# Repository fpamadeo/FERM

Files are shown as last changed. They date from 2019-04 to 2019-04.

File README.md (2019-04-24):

# F.E.R.M.

## UIC ECE Senior Design 2018-2019

_______________________________________________________________________________________________________________________________
## Table of Contents:
**FERMix** | **Fryer**
:---: | :---
**1** | [Members](README.md#1-Members)
**2** | [About the Project](README.md#2-About-the-Project)
2.1 | [Abstract](README.md#21-Abstract)
2.2 | [Project Overview](README.md#22-Project-Overview)
2.3 | [Design Alternatives](README.md#23-Design-Alternatives)
2.4 | ["Final Design"](README.md#24-Final-design)
2.5 | [Conclusion](README.md#25-Conclusion)
**3** | [Construction Guide](README.md##3-Construction-Guide)
3.1 | [LCD Screen](README.md#31-LCD-Screen)
3.2 | [Ultrasonic Sensor](README.md#32-Ultrasonic-Sensor)
3.3 | [Motor Driver](README.md#33-Motor-Driver)
3.4 | [Keypad](README.md#34-keypad)
**4** | [Acknowledgements](README.md##4-Acknowledgements)
 
____________________________________________________________________
## 1. Members:
* Francis Paul Amadeo
* Erick Estrada
* Meshal Alsaeed
* Rami Muhammad
______________________________________________________
## 2. About the Project:
### 2.1 Abstract:
>The project aims to create an affordable system for all commercial-grade fryers. In regards to cook-time management, we wish to ease the cooks’ workload by automating the deep frying process. However, we do not want our project to interfere with their normal operation while frying. Our project would just be a failsafe so that the food does not get overcooked. To solve these objectives, we opted to go for a modular design, which will include the main system and extensions. The main system will be chain-driven. The extensions can be customized depending on the user’s needs and space. Also, this design will feature pre-set and configurable user settings. Thus, giving the cooks a less stressful environment, making them free to do more things in the kitchen. The system is designed primarily as a way to simplify and reduce the complexity of frying food for restaurants by taking into account the FDA’s regulations.

### 2.2 Project Overview:
>The goal is to build an add-on for restaurant deep fryers. This add-on would automate the lowering and raising of the frying basket, with the user inputting how long the deep frying will last. Due to the stressful environment of restaurant kitchens, there are lots of food that get  burned from being left alone for too long. With our add-on, food waste would be reduced in addition to simplifying the frying process for workers.

### 2.3 Design Alternatives:
**Mechanisms:**
>The Actuator would help decrease the bulkiness of our system. However, this would also limit the modularity of the system, compared to the chain driven design we opted for.
> 
>The Lead Screw would give us a high positioning accuracy, but would in turn, be inefficient. Furthermore, lead screws are significantly more expensive compare to the other designs we had in mind

**Sensors:**
>A magnetic switch would be a great sensor to detect when the fryer basket is on our hanger, since most likely the basket is made of metal. However, since the hanger is made of metal itself, we opted to not use a magnetic switch.
>
>Similar to a magnetic switch, an inductive sensor will detect when metal object is near it. But rather than having a 0 or 1 input, it can sense how far the nearest metal is. Unfortunately, we opted to use the sensor we already have on-hand so we could use the resources for elsewhere. Going forward, we would have went with this sensor.

### 2.4 "Final Design":
>For the final design, we are going  to use a chain-driven mechanism, with one of the links of the chains attached to a steel pipe with threaded ends. This end could then be attached to a various choice of connectors which in turn, be connected to other pipes and finally to the fryer basket hanger. This gives the user the ability to customize the connections in accordance with their need. Furthermore, other than the basic timer option, the system gives the user the options to save up to three preset times and to calibrate the depth of the fryer vat.

### 2.5 Conclusion:
>In hindsight, with the large mechanical aspect of our system, we would have benefited with consulting with more mechanical engineers with our design. We would have also hoped to be able to test our other design alternatives, and be able to pick which one is the best.
> 
>Going forward, we have some design changes in order to improve the overall functionality and appearance of the system. These changes would include: a mechanism to prevent the chain from slacking as weight is added to the system; inductive sensing instead of ultrasonic; metal housing; a more permanent wiring and circuit layout and; other relatively minor issues we have yet to tackle due to time and financial constraints. 

______________________________________________________
## 3. Construction Guide:
* We are using an Arduino Mega (Elegoo MEGA2560 R3)
* We are using the MD10C R3 Motor Driver
### 3.1 LCD Screen:
Arduino | 2x16 LCD 
--- | ---
GND | VSS
5V | VDD
GND -> 1kOhm Resistor | VO
D12 | RS
GND | RW
D11 | E 
D23 | DB0
D27 | DB1
D31 | DB2
D35 | DB3
D34 | DB4
D30 | DB5
D26 | DB6
D22 | DB7
5V -> 224Ohm | A
GND | K

### 3.2 Ultrasonic Sensor:
Arduino | HC-SR04 
--- | ---
GND | GND
D48 | ECHO
D49 | TRIGGER
5V | VCC

### 3.3 Motor Driver:
Arduino | MD10C R3
--- | ---
GND | GND
D13 | PWM
D53 | DIR

### 3.4 Keypad:
Arduino | Keypad
--- | ---
D2 | 1
D3 | 2
D4 | 3
D5 | 4
D6 | 5
D7 | 6
D8 | 7
D9 | 8

***\*Keypad pins are numbered left to right, from the POV of looking at the back upright\****

______________________________________________________
## 4. Acknowledgements:
>Team F.E.R.M. would like to thank: the staff of UIC’s Makerspace; the members of Chicago Engineering Design Team; Mona Hurt and; our advisor, Dr. Wenjing Rao.

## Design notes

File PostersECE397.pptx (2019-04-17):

## FERMix Francis Amadeo, Erick Estrada, Rami Muhammed, Meshal Alsaeed, Advisor: Dr. Wejing Rao

Abstract

The project aims to create an affordable system for all commercial-grade fryers. In regards to cook-time management, we wish to ease the cooks’ workload by automating the deep frying process. However, we do not want our project to interfere with their normal operation while frying. Our project would just be a failsafe so that the food does not get overcooked. To solve these objectives, we opted to go for a modular design, which will include the main system and extensions. The main system will be chain-driven. The extensions can be customized depending on the user’s needs and space. Also, this design will feature pre-set and configurable user settings. Thus, giving the cooks a less stressful environment, making them free to do more things in the kitchen. The system is designed primarily as a way to simplify and reduce the complexity of frying food for restaurants by taking into account the FDA’s regulations.

Project Overview

Engineering Requirements

- The device should be able to operate from a 12V source
- The system should move the frying basket up and down in a range of 1.5 ft
- No part of the system should ever be dipped in the oil
- System should be easily disassembled with the use of handheld tools.
- The system will have a 4x4 keypad user-interface

Final Design

Design Alternatives

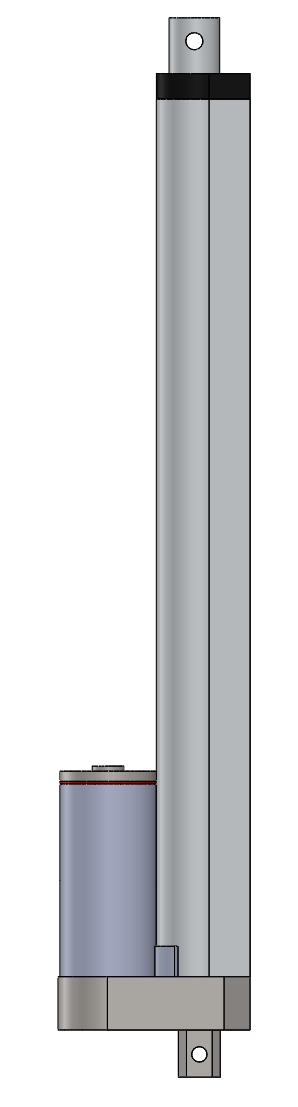
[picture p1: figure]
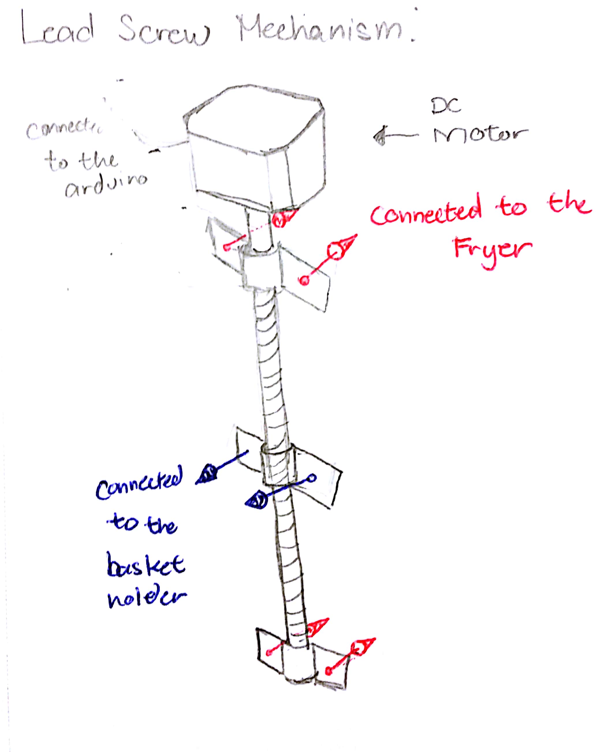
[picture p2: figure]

Testing & Results

Mechanisms:

Sensors:

Actuator

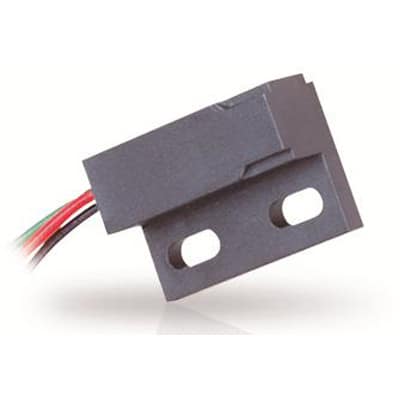
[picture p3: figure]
ZF Electronics MP102103

Magnetic switch

Lead Screw

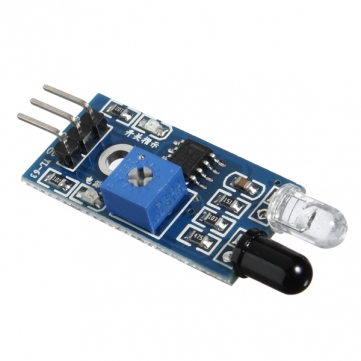
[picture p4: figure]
Image result for infrared proximity sensor arduino

Infrared
Proximity

Conclusion

Acknowledgements

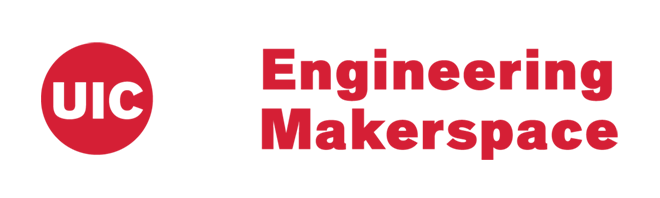
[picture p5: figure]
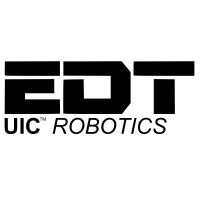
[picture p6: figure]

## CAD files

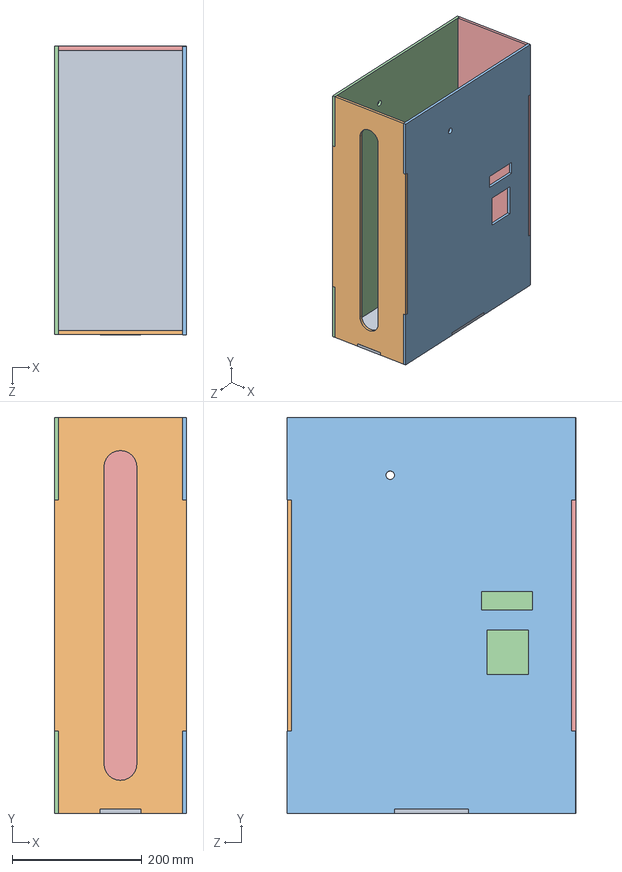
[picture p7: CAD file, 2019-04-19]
CAD/allpartstogether.SLDASM
203.4 x 609.9 x 444.7 mm
bottompanel
frontpanel
rightpanel
leftpanel
backpanel

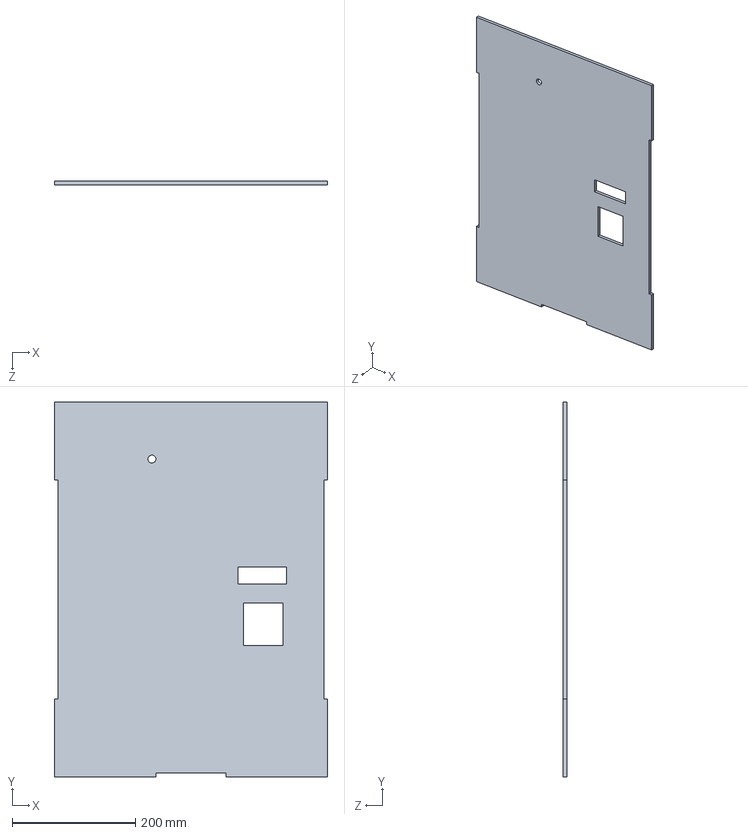
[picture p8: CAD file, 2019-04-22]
CAD/rightpanel.SLDPRT
444.5 x 609.6 x 6.35 mm

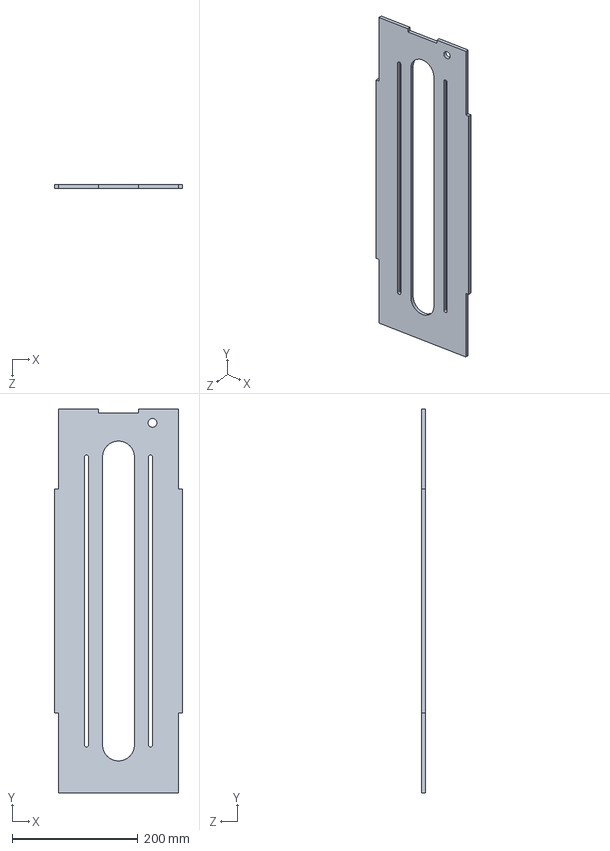
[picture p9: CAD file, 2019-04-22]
CAD/frontpanel.SLDPRT
203.2 x 609.6 x 6.35 mm

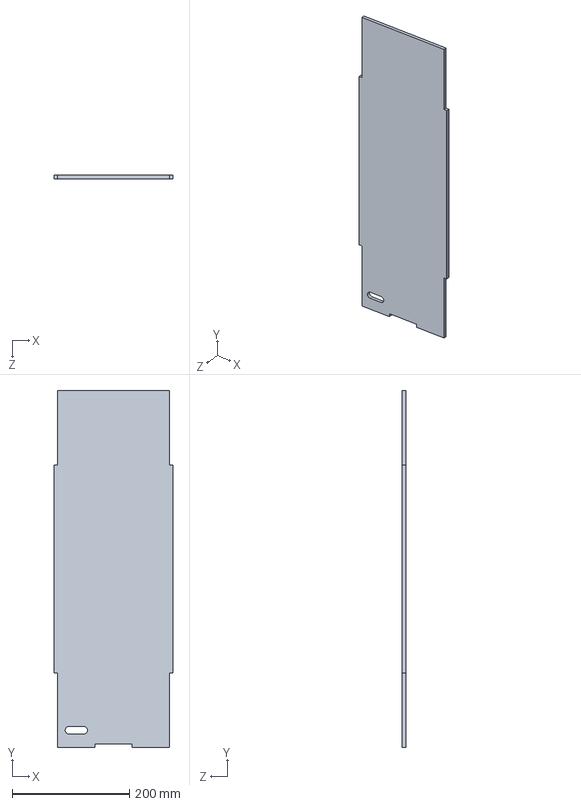
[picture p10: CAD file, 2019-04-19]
CAD/backpanel.SLDPRT
203.2 x 609.6 x 6.35 mm

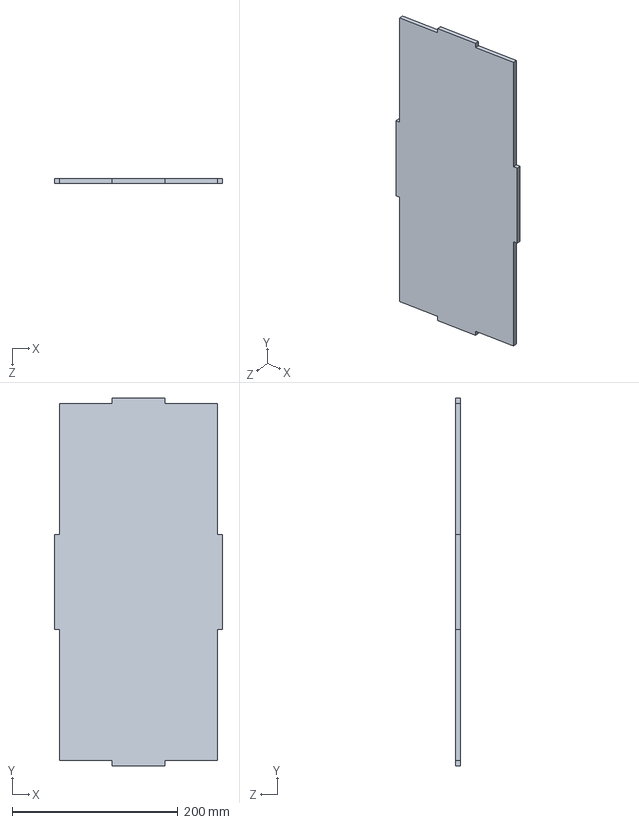
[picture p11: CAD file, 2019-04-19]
CAD/bottompanel.SLDPRT
203.2 x 444.5 x 6.35 mm

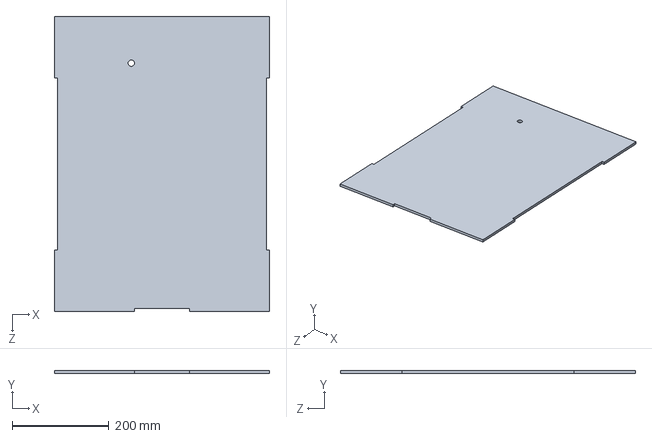
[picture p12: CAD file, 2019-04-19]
CAD/leftpanel.SLDPRT
444.5 x 6.35 x 609.6 mm

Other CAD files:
CAD/backpanel.DXF
CAD/bottompanel.DXF
CAD/frontpanel.DXF
CAD/leftpanel.DXF
CAD/rightpanel.DXF

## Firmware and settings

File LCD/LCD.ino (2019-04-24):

#include <LiquidCrystal.h>
#include <Wire.h>
#include <Keypad.h>
//**********************************************************************************************************//
//Preset:
String preset[3] = {"0015","0030","0100"}; //"MMSS" //Preset times

//LCD pins:
const int rs = 12, en = 11, d0 = 23, d1 = 27, d2 = 31, d3 = 35, d4 = 34, d5 = 30, d6 = 26, d7 = 22;
LiquidCrystal lcd(rs, en, d0, d1, d2, d3, d4, d5, d6, d7);

//MOTOR:
#define pwmPin 13 //Pin to send how fast it is
#define dirPin 53 //Pin to send if going clockwise or counter-clockwise
#define UP true //boolean value to send to move up
#define DOWN false //boolean value to send to move down
#define MOTOR_DELAY 200 //how long is each "step"; in microseconds
#define MOTOR_SPEED 255 //PWM value to send to motor driver; Range: 0-255
#define DEFAULT_STEPS 10//From lowest point to highest point in steps

//ULTRASONIC(US)  SENSOR:
#define echoPin 48 //ECHO
#define trigPin 49 //TRIGGER
#define sensorDelay 50 //centiseconds 
#define sensorThres 10 //threshold 

//Keypad:
const byte ROWS = 4; //How many rows are there in the keypad
const byte COLS = 4; //How many columns are there in the keypad

char keys[ROWS][COLS] =  //Mapping out the corresponding characters for each key
{
  {'1','2','3','A'},
  {'4','5','6','B'},
  {'7','8','9','C'},
  {'*','0','#','D'}
};

byte rowPins[ROWS] = {9, 8, 7, 6}; 
byte colPins[COLS] = {5, 4, 3, 2};

Keypad userKeypad = Keypad(makeKeymap(keys), rowPins, colPins, ROWS, COLS);

//GLOBAL Variables:

//Strings:
String timeIN = "0000"; //Time input in by the user for "normal" executions
String tempTime = "0000"; //Time input in by the user for "shift" executions; ##TODO: Might be redundant##

//Ints
int timeLeft = 0; //The actual time the user enters; should always be in seconds
int selected = 0; //The preset the user selected to be changed
int blinkDelay = 0; //Used to make the timer blink every 1 second
long duration;     //How long til the signal comes back
int distance;      //How far til the signal bounces off of something
int stepsToDo = DEFAULT_STEPS; //Steps needed for now #TODO#
int tempSteps = 0; //Steps the user is doing before everything is saved or cancelled 

//Bool:
bool error = false; //USED TO CHECK FOR ERRORS, should never be true
bool cancel = false; //TRUE when user cancels current action/s
bool shift = false; //TRUE when user uses the shift key 
bool calibrate = false; //TRUE when the user is calibrating
bool changePreset = false; //TRUE when the user is changing a preset
bool blinkTime = false; //USED FOR MAKING THE TIME BLINK every 1 second 

//**********************************************************************************************************//
//SETUP
void setup() 
{
  //US SENSOR:
  pinMode(trigPin, OUTPUT); // Sets the trigPin as an Output
  pinMode(echoPin, INPUT); // Sets the echoPin as an Input

  //MOTOR:
  pinMode(dirPin, OUTPUT);
  digitalWrite(dirPin, HIGH);//initialization
  analogWrite(pwmPin, 0); //initialization
  stepsToDo = DEFAULT_STEPS;
   
  //TESTING:
  Serial.begin(9600);

  //LCD:
  // set up the LCD's number of columns and rows:
  lcd.begin(16, 2);
  // Print a message to the LCD.
  lcd.print("Standby");
  lcd.setCursor(11,0);    
  lcd.print("TIME:");
  lcd.setCursor(11,1);    
  lcd.print(timeIN[0]);
  lcd.print(timeIN[1]);
  lcd.print(":");
  lcd.print(timeIN[2]);
  lcd.print(timeIN[3]);
}

//**********************************************************************************************************//
//Previous Code:
/*
//MOTOR GO UP
void moveUp(){
  digitalWrite(dirPin, HIGH);
  analogWrite(pwmPin, 255);
  delay(100);
}

//MOTOR GO DOWN
void moveDown(){
  digitalWrite(dirPin, LOW);
  analogWrite(pwmPin, 255);
  delay(100);
}
*/

//MOVE MOTOR:
void moveMotor(bool dir, int steps){
  int eachDelay;
  if (steps < 1){
    error = true;
    updateScreen(); //Show on screen, there's error
    delay(3000);
    updateScreen(); //Return to standby, after three second
    return;
  }
  if (dir == UP){
    digitalWrite(dirPin, LOW);
    eachDelay = MOTOR_DELAY;
  }
  else{
    digitalWrite(dirPin, HIGH);
    eachDelay = MOTOR_DELAY * 80 / 100;
  }
  analogWrite(pwmPin, MOTOR_SPEED);
  delay(eachDelay * (steps));
  //analogWrite(pwmPin, MOTOR_SPEED / 2);
  //delay(MOTOR_DELAY);
  analogWrite(pwmPin, 0);
  return;
}

//**********************************************************************************************************//
//UPDATES JUST TIME
void updateTime(){
  //lcd.setCursor(0,1);
  //lcd.print(timeLeft);
  int minutes, seconds;
  if(cancel){
    return;
  }
  minutes = timeLeft / 60;
  seconds = timeLeft % 60;
  if(minutes > 99){
    minutes = 99;
  }
  lcd.setCursor(11,1);    
  lcd.print(minutes/10);
  lcd.print(minutes%10);
  lcd.print(":");
  lcd.print(seconds/10);
  lcd.print(seconds%10);
  delay(1000);
}

//UPDATES DISPLAY
void updateScreen(){
  if (error){
    error = false;
    lcd.setCursor(11,1);
    lcd.print("ERROR");
    delay(1000);
  }
  if (cancel){
    cancel = false;
    lcd.setCursor(11,1);
    lcd.print("CNCEL");
    lcd.setCursor(0,0);
    lcd.print("Standby    ");
    lcd.setCursor(0,1);
    lcd.print("           ");
    delay(500);
  }
  lcd.setCursor(0,1);
  if (changePreset){
    lcd.print("Preset");
    lcd.print(" ");
  }
  if (selected != 0){
    lcd.print(selected);
    lcd.print(" ");
  }
  if (shift){
    lcd.print("S");
  }
  if (timeLeft <= 0 or cancel){
    lcd.setCursor(11,1);    
    lcd.print(timeIN[0]);
    lcd.print(timeIN[1]);
    lcd.print(":");
    lcd.print(timeIN[2]);
    lcd.print(timeIN[3]);
  }
  else{
    lcd.setCursor(0,0);
    lcd.print("ON         ");
  }
}

//**********************************************************************************************************//
//GIVES PROPER INT FOR CASES:
String getInt(char input){
  if (input == '*'){
    return "10";
  }
  if (input == '#'){
    return "11";
    }
  if (input == 'A'){
    return "12";
  }
  if (input == 'B'){
    return "13";
    }
  if (input == 'C'){
    return "14";
  }
  if (input == 'D'){
    return "15";
  }
  String returnThis = "";
  returnThis += input;
  return returnThis;
}

//**********************************************************************************************************//

//CHECKS SENSOR IF THERE IS SOMETHING THERE //#TODO: FIND DECENT NUMBER FOR THE BASKET#//
bool checkSensor(bool motorPosition){

  for(int i = 0; i < sensorDelay; i++){
       // Clears the trigPin
      digitalWrite(trigPin, LOW);
      delayMicroseconds(2);
      // Sets the trigPin on HIGH state for 10 micro seconds
      digitalWrite(trigPin, HIGH);
      delayMicroseconds(10);
      digitalWrite(trigPin, LOW);
      // Reads the echoPin, returns the sound wave travel time in microseconds
      duration = pulseIn(echoPin, HIGH);
      // Calculating the distance
      distance= duration*0.034/2;
      // Prints the distance on the Serial Monitor
      Serial.print("Duration: ");
      Serial.println(duration);
      Serial.print("Distance: ");
      Serial.println(distance);
      if (motorPosition == UP){
        if (distance < sensorThres){
          return false;
        }
      }
      else{
        if (distance < sensorThres){
          return true;
        }
      }
      
  }
  if (motorPosition == UP){
        return true;
   }
  else{
        return false;
    }
}

//**********************************************************************************************************//
//CHECKS KEY AND CORRESPONDS THE RIGHT ACTION
void checkKey(int input){
  switch(input){
   case 11: //Cancel?
      //Use Function to cancel timer here
      cancel = true;
      timeIN = "0000";
      timeLeft = 0;
      
      updateScreen();
      break;
   case 12: //Shift fn?
      shift = true;
      updateScreen();
      //lcd.setCursor(0,0);
      //lcd.print("SHIFT");
      break;case 13: //Preset 1?
      lcd.setCursor(0,0);
      timeIN = preset[0];
      updateScreen();
      break;
   case 14: //Preset 2?
      lcd.setCursor(0,0);
      timeIN = preset[1];
      updateScreen();
      break;
   case 15: //Preset 3?
      lcd.setCursor(0,0);
      timeIN = preset[2];
      updateScreen();
      break;
    case 1:
    case 2:
    case 3:
    case 4:
    case 5:
    case 6:
    case 7:
    case 8:
    case 9:
    case 0:
      //Remove the first char of the string and add the input at the end:
      timeIN.remove(0,1);
      timeIN += input;
  
      updateScreen();
      break;
   case 10: //Enter?
      //use function to start timer here
      String toNum = "";
      toNum += timeIN[0];
      toNum += timeIN[1];
      timeLeft =  toNum.toInt() * 60;
      toNum = "";
      toNum += timeIN[2];
      toNum += timeIN[3];
      timeLeft = timeLeft + toNum.toInt();
      timeIN = "0000";
      updateScreen();
      break;
   default: 
      error = true;
      break;
  }
}

//CHECKS KEY AND CORRESPONDS THE RIGHT SHIFT ACTION
void checkShift(int input){
  //lcd.print(input);
  switch(input){
    case 1://Calibration
      if(not changePreset){
        calibrate = true;
        lcd.setCursor(0,0);
        lcd.print("Calibrate  ");
        updateScreen();
      }
      break;
    case 2:
      if (calibrate){
        moveMotor(UP, 1);
        tempSteps--;
      }
      break;
    case 5:
      if (calibrate){
        moveMotor(DOWN,1);
        tempSteps++;
      }
      break;
    case 4://Change Preset
      if(not calibrate){
        changePreset = true;
        lcd.setCursor(0,0);
        lcd.print("Changing ");
        updateScreen();
      }
      break;
    case 10: //Enter?
      calibrate = false;
      changePreset = false;
      shift = false;
      if (tempSteps < 0){
        tempSteps--;
      }
      else if (tempSteps > 0){
        tempSteps++;
      }
      stepsToDo += tempSteps;
      tempSteps = 0;
      lcd.setCursor(0,0);
      lcd.print("Saved      ");
      delay(500);
      lcd.setCursor(0,0);
      lcd.print("Standby    ");
      lcd.setCursor(0,1);
      lcd.print("           ");
      break;
   case 11: //Cancel?
      if(tempSteps > 0){
        for(int i = 1; i <= tempSteps; i++){
          moveMotor(UP, 1);
          delay(100);
        }
      }
      else if(tempSteps == 0){
        
      }
      else{
        for(int i = 1; i <= (tempSteps*-1) ; i++){
          moveMotor(DOWN, 1);
          delay(100);
        }
      }
      tempSteps = 0;
      calibrate = false;
      changePreset = false;
      shift = false;
      lcd.setCursor(0,0);
      lcd.print("Cancelled  ");
      delay(500);
      lcd.setCursor(0,0);
      lcd.print("Standby    ");
      lcd.setCursor(0,1);
      lcd.print("           ");
      
      break;
   case 13: //Preset 1?
      if(changePreset){
        selected = 1;
        tempTime = "0000";
      }
      updateScreen();
      break;
   case 14: //Preset 2?
      if(changePreset){
        selected = 2;
        tempTime = "0000";
      }
      updateScreen();
      break;
   case 15: //Preset 3?
      if(changePreset){
        selected = 3;
        tempTime = "0000";
      }
      updateScreen();
      break;
   default:
      break;
  }
}

//Uses the whole keypad again, for changing presets
void changeSelected(int input){
  if (changePreset){
      switch(input){
       case 13: //Preset 1?
          if(changePreset){
            selected = 1;
            tempTime = "0000";
          }
          updateScreen();
          break;
       case 14: //Preset 2?
          if(changePreset){
            selected = 2;
            tempTime = "0000";
          }
          updateScreen();
          break;
       case 15: //Preset 3?
          if(changePreset){
            selected = 3;
            tempTime = "0000";
          }
          updateScreen();
          break;
        case 11: //Cancel?
          //Use Function to cancel timer here
          selected = 0;
          shift = false;
          lcd.setCursor(0,0);
          lcd.print("Cancellled  ");
          lcd.setCursor(0,1);
          lcd.print("           ");
          tempTime = "0000";
          updateScreen();
          break;
        case 1:
        case 2:
        case 3:
        case 4:
        case 5:
        case 6:
        case 7:
        case 8:
        case 9:
        case 0:
          //Remove the first char of the string and add the input at the end:
          //if(tempTime[selected-1] == "0"){
            tempTime.remove(0,1);
            tempTime += input;
          //}
          //else{
          //  error = true;
          //}
          updateScreen();
          break;
       case 10: //Enter?
          //use function to start timer here
          preset[selected-1] = tempTime;
          lcd.setCursor(0,0);
          lcd.print("DONE       ");
          lcd.setCursor(0,1);
          lcd.print("           ");
          shift = true;
          selected = 0;
          tempTime = "0000";
          break;

       default:
          error = true;
          break;
    }
  }
}

//**********************************************************************************************************//
//MAIN:
void loop() 
{
  //Getting input; customKey == NULL if there is none
  char customKey = userKeypad.getKey();
  //Check if there's an interrupt or there is time left:
  if (customKey){
    String caseKey = "";
    caseKey += getInt(customKey);
    int caseKeyInt = caseKey.toInt();
    Serial.println(customKey);
    
    //lcd.setCursor(0,0);
    //lcd.print(customKey);
    //lcd.print(":");
    //lcd.print(caseKeyInt);
    
    if (not shift){
       checkKey(caseKeyInt);
    }
    else{
      if(selected == 0){
        checkShift(caseKeyInt);
      }
      else{
        changeSelected(caseKeyInt);
      }
    }
  }

 if (timeLeft > 0){
    updateTime();
    timeLeft--;
    if (timeLeft == 0){
      lcd.setCursor(15,1);
      lcd.print("0");
      if(checkSensor(DOWN)){
        for(int i = 0; i < stepsToDo; i++){
          moveMotor(UP, 1);
          delay(10);
        }
        Serial.print("FRYER'S THERE");
        delay(500);
        lcd.setCursor(0,0);
        lcd.print("Hanger Up  ");
        lcd.setCursor(0,1);
        lcd.print("           ");
        while(not checkSensor(UP)){
        //  delay(200); //loop while basket is there
        }
        for(int i = 0; i < stepsToDo; i++){
          moveMotor(DOWN, 1);
          delay(10);
        }
      }
      else{
        lcd.setCursor(0,0);
        lcd.print("NO BASKET");
        delay(500);
      }
      lcd.setCursor(0,0);
      lcd.print("Standby  ");
      lcd.setCursor(0,1);
      lcd.print("           ");      
    }
 }
 if (changePreset){
    if (blinkTime){    
      lcd.setCursor(11,1);    
      lcd.print(tempTime[0]);
      lcd.print(tempTime[1]);
      lcd.print(":");
      lcd.print(tempTime[2]);
      lcd.print(tempTime[3]);
      if(blinkDelay >= 500){
        blinkTime = false;
        blinkDelay = 0;
      }
      else{
        blinkDelay++;
      }
    }
    else{
      lcd.setCursor(11,1);    
      lcd.print("     ");
      if(blinkDelay >= 500){
        blinkTime = true;
        blinkDelay = 0;
      }
      else{
        blinkDelay++;
      }
    }
 }

}

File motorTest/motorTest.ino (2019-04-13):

void setup() 
{
  pinMode(2, OUTPUT);
  // put your setup code here, to run once:

}

void loop() 
{
analogWrite(13, 255);






/*for (int i=0; i <= 255; i++)
{
      analogWrite(13, i);
      //delay(5000);
 }
delay(5000);


for (int i=255; i >= 255; i--)
{
      analogWrite(13, i);
      //delay(5000);
 }
delay(5000);
*/
/*
delay(500);
digitalWrite(1, HIGH);
analogWrite(13, 255);
delay(500);
analogWrite(13, 200);
delay(500);
analogWrite(13, 150);
delay(500);
analogWrite(13, 100);
delay(500);
analogWrite(13, 50);
delay(500);
analogWrite(13, 0);
delay(500);
*/

 /*
delay(1000);

digitalWrite(1, LOW);
for(int i=0; i<=255; i++)
{
  analogWrite(13, i);
  delay(10);
}
/////////
*/



/*
digitalWrite(1, HIGH);
for(int i=255; i>=0; --i)
{
  analogWrite(13, i);
  delay(10);
}

delay(2000);


digitalWrite(1, LOW);
for(int i=0; i<=0; i++)
{
  analogWrite(13, i);
  delay(10);
}

delay(3000);

/*
digitalWrite(1, LOW);
analogWrite(13, 0);
delay(500);
analogWrite(13, 50);
delay(500);
analogWrite(13, 100);
delay(500);
analogWrite(13, 150);
delay(500);
analogWrite(13, 200);
delay(500);
analogWrite(13,255);
delay(3000);
*/

/*
digitalWrite(1, HIGH);
for (int i = 255; i >= 0; --i) 
{
  analogWrite(13, i);
  delay(500);
}
 delay(2500);
 digitalWrite(1, LOW);

 for (int i= 0; i <=0; i++) 
{
  analogWrite(13, i);
  delay(500);
}
 delay(2500);
*/

/*
//delay(1000);
digitalWrite(1, LOW);

for (int i=0; i <= 255; i++)
{
  
      analogWrite(13, i);
      i=i+50;
    
 }
delay(2500);

*/


/*digitalWrite(1, LOW);
analogWrite(13, 50);
delay(500);
analogWrite(13, 100);
delay(500);
analogWrite(13, 150);
delay(500);
analogWrite(13, 200);
delay(500);
analogWrite(13, 255);
delay(10000);
//analogWrite(13, 0);
//delay(1000);
*/
 

  
  // put your main code here, to run repeatedly:

}

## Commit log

2019-04-13 Preset and Motor works
2019-04-24 4/24/19 Morning update... Pre-assembly code
